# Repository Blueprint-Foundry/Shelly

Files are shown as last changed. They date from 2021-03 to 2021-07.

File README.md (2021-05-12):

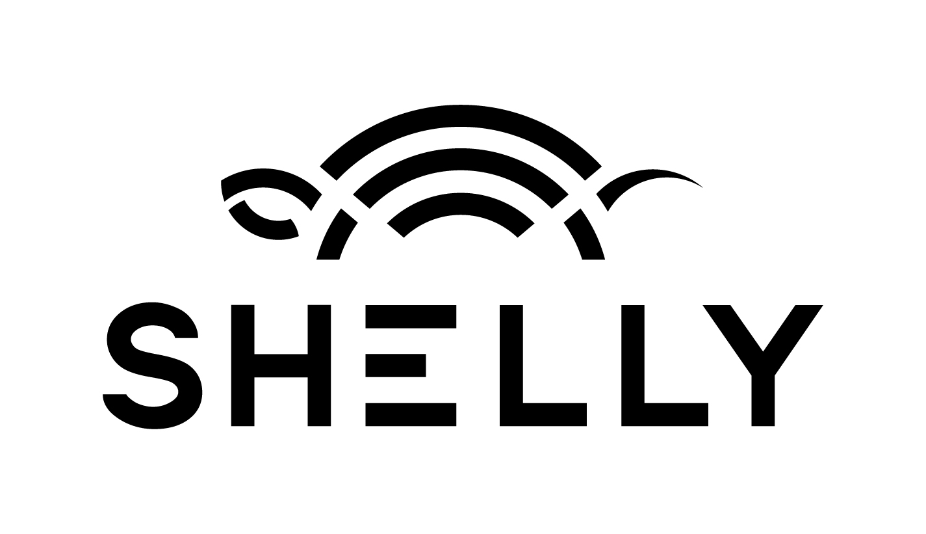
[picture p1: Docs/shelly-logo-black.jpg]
Shelly

Shelly aims to be a low cost ROS robot for teaching and R&amp;D for makers, universities and corporations.



## Links
* Circuitmaker page for the Hardware: https://workspace.circuitmaker.com/Projects/Details/Ilia-Baranov/Shelly

## Dependencies
These must be installed to your environment
* ESP32 Arduino Board Manager https://github.com/espressif/arduino-esp32/blob/master/docs/arduino-ide/boards_manager.md
* Arduino Library https://github.com/bblanchon/ArduinoJson
* Arduino Library https://github.com/Links2004/arduinoWebSockets
* Arduino Library https://github.com/Blueprint-Foundry/Arduino-MAX17055_Driver
* Arduino Library https://github.com/Blueprint-Foundry/PI4IOE5V96248_Arduino_Library
* Arduino Library https://github.com/Blueprint-Foundry/EAAPMST3923A2_Arduino_Library
* Arduino Library https://github.com/pololu/vl53l1x-arduino.git
* Arduino Library https://github.com/sparkfun/SparkFun_ICM-20948_ArduinoLibrary
(note: ensure to enable DMP functionality. Edit ICM_20948_C.h and uncomment line 29: #define ICM_20948_USE_DMP

## Licenses
* Hardware is licensed under Attribution-NonCommercial 4.0 International (CC BY-NC 4.0): https://creativecommons.org/licenses/by-nc/4.0/
* Software is licensed under BSD 3 Clause: https://opensource.org/licenses/BSD-3-Clause
* Documentation is licensed under Attribution-ShareAlike 2.0 Generic (CC BY-SA 2.0): https://creativecommons.org/licenses/by-sa/2.0/
* This project intends to submit for Open Source Hardware certification once ready, this certification mark will be added once successfully granted. https://certification.oshwa.org/
* All rights reserved by Blueprint Foundry.

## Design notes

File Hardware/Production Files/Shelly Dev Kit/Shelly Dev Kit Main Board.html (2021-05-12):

Altium

# Board Information

Date: | | 5/12/2021
Time: | | 10:19:24 AM
Elapsed Time: | | 00:00:00
Filename: | | Shelly Dev Kit Main Board.CMPcbDoc
Units: | | mmmils

General
Horizontal Dimension, max | 3505mils
Vertical Dimension, max | 2125mils
Total surface area
Copper layer count | 2
Smallest electrical gap/space | -
Smallest track width | 1.969mils
Smallest hole size | 12mils
Biggest hole size | 40mils
Number of plated through holes | 182
Number of plated slots | 4
Number of unplated holes | 0
Number of unplated slots | 0
Number of cutouts | 1

Back to top

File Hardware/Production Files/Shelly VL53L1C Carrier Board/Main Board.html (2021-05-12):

Altium

# Board Information

Date: | | 5/12/2021
Time: | | 10:23:28 AM
Elapsed Time: | | 00:00:00
Filename: | | Main Board.CMPcbDoc
Units: | | mmmils

General
Horizontal Dimension, max | 14.5mm
Vertical Dimension, max | 16.5mm
Total surface area
Copper layer count | 2
Smallest electrical gap/space | -
Smallest track width | 0.05mm
Smallest hole size | 0.3048mm
Biggest hole size | 1.016mm
Number of plated through holes | 20
Number of plated slots | 0
Number of unplated holes | 0
Number of unplated slots | 0
Number of cutouts | 1

Back to top

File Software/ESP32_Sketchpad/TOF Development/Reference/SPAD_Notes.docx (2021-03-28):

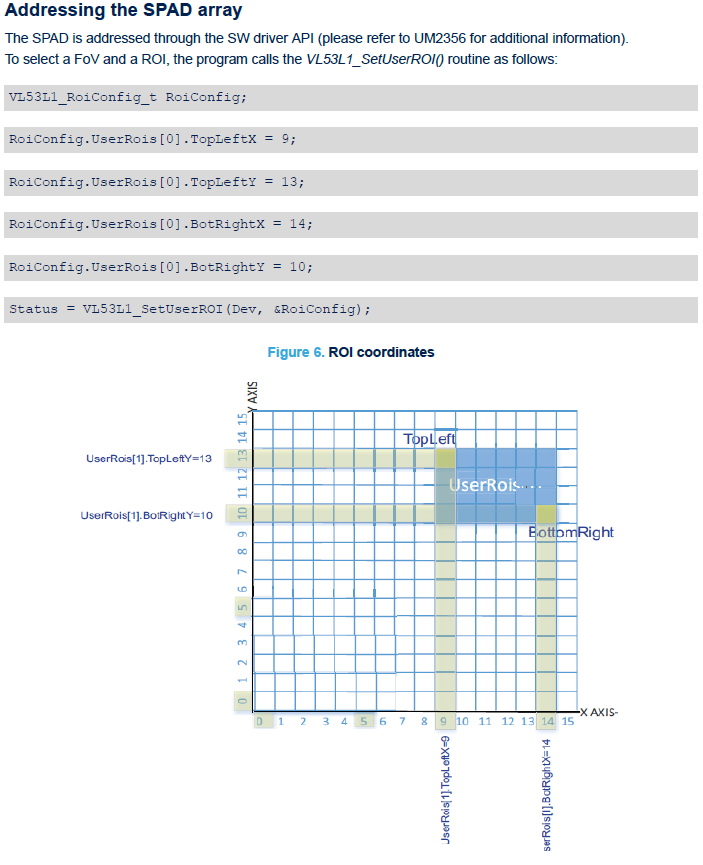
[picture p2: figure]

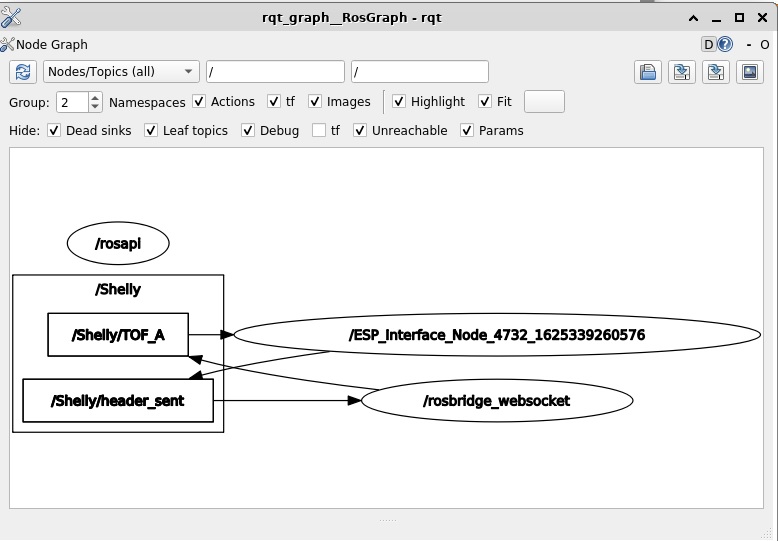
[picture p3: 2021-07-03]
Software/ESP32 Sketchpad/TOF Development/rqt_graph_ESP_interface_node.jpg

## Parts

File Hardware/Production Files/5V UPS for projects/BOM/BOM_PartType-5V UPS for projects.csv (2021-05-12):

Comment | Description | Designator | Quantity | DNP | Octopart URL
Battery | Battery Lithium 3.7V 2.6AH | BT1 | 1 | DNP
Samsung CL10A475MQ8NNNC | CL10 Series 4.7 uF 6.3 V ±20 % Tolerance X5R SMT Multilayer Ceramic Capacitor | C1, C2, C3, C4, C5, C10 | 6 |  | https://octopart.com/cl10a475mq8nnnc-samsung-19831531
Samsung CL05A104KA5NNNC | Ceramic capacitor SMD-0402 100nF /25V X5R# K +-10%, Samsung, RoHS | C6, C11 | 2 |  | https://octopart.com/cl05a104ka5nnnc-samsung-19018960
Samsung Electro-Mechanics CL21A226MOCLRNC | Cap Ceramic 22uF 16V X5R 20% SMD 0805 85°C Cardboard T/R | C7, C8, C9 | 3
Samsung CL05Y474KP5VPNC | Capacitor Ceramic 0.47uF 10% 10V 2-Pin Surface Mount T/R | C12, C13 | 2 |  | https://octopart.com/cl05y474kp5vpnc-samsung-106864824
LTST-C190TBKT | Standard LEDs - SMD WL-SMCD SMD Mono SMD 0603 Blue 465nm | D1 | 1
Lite-On LTST-C190EKT | LED; SMD; 0603; red; 1.12-3mcd; 1.6x0.8x0.8mm; 130°; 2÷2.6V; 10mA | D2 | 1
Lite-On LTST-C190GKT | Green 1.6 x 0.8 x 0.8 mm 130° Water Clear 6 mcd 2.1 V Surface Mount LED | D3 | 1
CUI TB003-500-P02BE | Terminal Block, Screw Type, 5.00 | J1, J2, J5 | 3 |  | https://octopart.com/tb003-500-p02be-cui-100131675
Keystone 54 | Cylindrical Battery Contacts, Clips, Holders & Springs 16-19mm PC BATTERY CLIP | J3, J6 | 2
Adam Tech PH1-05-UA | Conn Unshrouded Header HDR 5 POS 2.54mm Solder ST Thru-Hole | J4 | 1 | DNP | https://octopart.com/ph1-05-ua-adam+tech-7873130
10118194-0001LF | Single Port 5 Contact Horizontal Right Angle Micro B USB 2.0 Receptacle | K1 | 1
Bourns SRN5040TA-1R5M | Ind Power Wirewound 1.5uH 20% Ferrite Core T/R | L1 | 1 |  | https://octopart.com/srn5040ta-1r5m-bourns-95745279
MMBT3906-7-F | MMBT3906 Series PNP 40 V 300 mW Small Signal Transistor Surface Mount- SOT-23-3 | Q1 | 1 |  | https://octopart.com/mmbt3906-7-f-diodes+inc.-39667659
MCU80N03A-TP | N-channel Mosfet, Dpak Package | Q2 | 1 |  | https://octopart.com/mcu80n03a-tp-mcc-110117594
Stackpole Electronics RMCF0603ZT0R00 | RMCF Series 0603 0.1 W 0 Ohm Jumper Surface Mount Thick Film Chip Resistor | R1, R7 | 2 |  | http://octopart.com/rmcf0603zt0r00-stackpole+electronics-19213618
Stackpole Electronics RMCF0402FT3K90 | Res Thick Film 0402 3.9K Ohm 1% 1/16W ±100ppm/°C Molded SMD SMD Paper T/R | R2 | 1 |  | https://octopart.com/rmcf0402ft3k90-stackpole+electronics-21527179
Stackpole Electronics RMCF0603JT680R | Res Thick Film 0603 680 Ohm 5% 0.1W(1/10W) ±200ppm/C Pad SMD Automotive T/R | R3, R6, R8 | 3 |  | https://octopart.com/rmcf0603jt680r-stackpole+electronics-19213592
Stackpole Electronics RMCF0402FT22K1 | Res Thick Film 0402 22.1K Ohm 1% 0.063W ±100ppm/°C Molded SMD Paper T/R | R4, R12 | 2 |  | https://octopart.com/rmcf0402ft22k1-stackpole+electronics-19211363
Stackpole Electronics RMCF0402FT511R | Res Thick Film 0402 511 Ohm 1% 0.063W(1/16W) ±100ppm/C Pad SMD Automotive T/R | R5, R11 | 2 |  | https://octopart.com/rmcf0402ft511r-stackpole+electronics-19212568
Stackpole Electronics RMCF0603FT2K00 | Res Thick Film 0603 2K Ohm 1% 0.1W(1/10W) ±100ppm/C Pad SMD Automotive T/R | R9 | 1 |  | https://octopart.com/rmcf0603ft2k00-stackpole+electronics-19213115
Stackpole Electronics RMCF0402FT2K55 | Res Thick Film 0402 2.55K Ohm 1% 0.063W ±100ppm/°C Molded SMD Paper T/R | R10 | 1 |  | https://octopart.com/rmcf0402ft2k55-stackpole+electronics-19211346
Stackpole Electronics RMCF0402FT33K0 | Res Thick Film 0402 33K Ohm 1% 0.063W(1/16W) ±100ppm/C Pad SMD Automotive T/R | R13 | 1 |  | https://octopart.com/rmcf0402ft33k0-stackpole+electronics-19212474
Stackpole Electronics RMCF0402FT2K00 | Res Thick Film 0402 2K Ohm 1% 0.063W(1/16W) ±100ppm/C Pad SMD Automotive T/R | R14 | 1 |  | https://octopart.com/rmcf0402ft2k00-stackpole+electronics-19212433
Stackpole Electronics RMCF0603FT215R | Res Thick Film 0603 215 Ohm 1% 0.1W(1/10W) ±100ppm/C Pad SMD Automotive T/R | R15 | 1 |  | https://octopart.com/rmcf0603ft215r-stackpole+electronics-19211080
Stackpole Electronics RMCF0402JT10K0 | Res Thick Film 0402 10K Ohm 5% 0.063W(1/16W) ±100ppm/C Pad SMD Automotive T/R | R16, R17 | 2 |  | https://octopart.com/rmcf0402jt10k0-stackpole+electronics-19212679
Cyntec RL1632T4F-R010-FNH | Res 0.01 Ohm 1% 1W 1206 | R18 | 1 |  | https://octopart.com/rl1632t4f-r010-fnh-cyntec-86610802
C&K Components OS102011MS2QN1 | Switch; Slide; Mini; SPDT; ON-ON; Non-Shorting(BBM); 100mA; 12VDC; ThruHole; PC Pin | SW1, SW2 | 2 |  | https://octopart.com/os102011ms2qn1-c%26k+components-2486956
TPS2121RUXR | 2.7-22V, 56m?, 4.5A, Priority Power MUX with Seamless Switchover 12-VQFN-HR -40 to 125 | U1 | 1 |  | https://octopart.com/tps2121ruxr-texas+instruments-95511053
Texas Instruments TPS259571DSGR | TPS259571 12V eFuse with Fast Overvoltage Protection 2.7V to 18V 4A 34m Ohm 8-Pin WSON T/R | U2 | 1 |  | https://octopart.com/tps259571dsgr-texas+instruments-88135752
MCP73831T-2DCI/OT | Microchip MCP73831T-2DCI/OT; Battery Charge Controller; 500mA; 5-Pin SOT-23 | U3 | 1 |  | https://octopart.com/mcp73831t-2dci%2Fot-microchip-422782
MAX17055ETB+T | MAX17055 Series 4.9 V 18 uA Stand-Alone ModelGauge m5 Fuel Gauge - TDFN-10 | U4 | 1 |  | https://octopart.com/max17055etb%2Bt-maxim+integrated-76519097
RT4812GJ8F | Boost Switching Regulator IC Positive Adjustable 1.8V 1 Output 2A SOT-23-8 Thin, TSOT-23-8 | U5 | 1

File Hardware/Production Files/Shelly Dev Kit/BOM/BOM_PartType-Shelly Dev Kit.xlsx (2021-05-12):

Comment | Description | Manufacturer Part Number | Octopart URL | Designator | Quantity | DNP
ESP32-WROVER-E (8MB) | Rx Txrx Mod Wifi Pcb Trace SMD | ESP32-WROVER-E (8MB) | https://octopart.com/esp32-wrover-e+%288mb%29-espressif+systems-108216292 | A1 | 1
Everlight EAAPMST3923A2 | Ambient Light Sensor | EAAPMST3923A2 |  | A2 | 1
1uF | CAP CER 1UF 16V 10% X5R 0603 |  | https://octopart.com/0603yd105kat2a-avx+interconnect+%2F+elco-46506197 | C1, C2, C3, C4, C5, C10, C13 | 7
Samsung Electro-Mechanics CL21A226MOCLRNC | Cap Ceramic 22uF 16V X5R 20% SMD 0805 85°C Cardboard T/R | CL21A226MOCLRNC |  | C6, C8, C12, C14 | 4
Taiyo Yuden TMK105BJ223KV-F | Multilayer Ceramic Capacitors (High dielectric type), 25V, 0.022 uF, ± 10 %, 0402, X5R/B, RoHS | TMK105BJ223KV-F | https://octopart.com/tmk105bj223kv-f-taiyo+yuden-23272753 | C7 | 1
Samsung CL05A104KA5NNNC | Ceramic capacitor SMD-0402 100nF /25V X5R# K +-10%, Samsung, RoHS | CL05A104KA5NNNC | https://octopart.com/cl05a104ka5nnnc-samsung-19018960 | C9, C11 | 2
Seeed Studio 601000200 | Address Led Discret Serial R/g/b | 601000200 | https://octopart.com/601000200-seeed+studio-88826571 | D1, D2 | 2
JST (JAPAN SOLDERLESS TERMINALS) B5B-XH-A(LF)(SN) | CONN HEADER XH TOP 5POS 2.5MM | B5B-XH-A(LF)(SN) | https://octopart.com/b5b-xh-a%28lf%29%28sn%29-jst-3990208 | J1 | 1
Global Connector Technology BG302-05-A-L-G | Board to Board, Receptacle, 5 Position, 1ROW | BG302-05-A-L-G | https://octopart.com/bg302-05-a-l-g-global+connector+technology-22009391 | J2 | 1
Amphenol ICC / FCI SFV24R-3STE1HLF | SFV24R-3STE1HLF-FFC/FPC Conn Rohs Compliant: Yes | SFV24R-3STE1HLF | https://octopart.com/sfv24r-3ste1hlf-amphenol+icc+%2F+fci-22289564 | J3 | 1
Adam Tech PH1-05-UA | Conn Unshrouded Header HDR 5 POS 2.54mm Solder ST Thru-Hole | PH1-05-UA | https://octopart.com/ph1-05-ua-adam+tech-7873130 | J4, J5 | 2 | DNP
10118194-0001LF | Single Port 5 Contact Horizontal Right Angle Micro B USB 2.0 Receptacle |  |  | K1 | 1
MMBT3904 | TRANS NPN 40V 0.2A SOT23 |  | https://octopart.com/mmbt3904%2C215-nxp+semiconductors-10477684 | Q1, Q2 | 2
Nexperia 2N7002NXAKR | 2N7002NXAK - 60 V, single N-channel Trench MOSFET | 2N7002NXAKR | https://octopart.com/2n7002nxakr-nexperia-103147780 | Q3, Q4 | 2
10k | RES SMD 10K OHM 5% 1/10W 0603 | RC1608J103CS | http://octopart.com/rc1608j103cs-samsung-2405586 | R1, R2, R5, R6, R7, R8, R9, R14, R15, R16, R17, R18, R19 | 13
27R | YAGEO (PHYCOMP) RC0603JR-0727RL RESISTOR, RC21 0603 27R |  | http://octopart.com/rc0603jr-0727rl-yageo-40953074 | R3, R4 | 2
Stackpole Electronics RMCF0402JT1K00 | Res Thick Film 0402 1K Ohm 5% 0.063W(1/16W) ±100ppm/C Pad SMD Automotive T/R | RMCF0402JT1K00 | https://octopart.com/rmcf0402jt1k00-stackpole+electronics-19212695 | R10, R13, R20 | 3
Ohmite KDV12DR200ET | 0.2 Ohm 1206 0.5% 0.5W Rohs Compliant: Yes | KDV12DR200ET | https://octopart.com/kdv12dr200et-ohmite-103743653 | R11, R12 | 2
C&K Components PTS636 SL50 SMTR LFS | Switch Tactile N.O. SPST Rectangular Button Gull Wing 0.05A 12VDC 1.27N SMD T/R | PTS636 SL50 SMTR LFS | https://octopart.com/pts636+sl50+smtr+lfs-c%26k+components-100131649 | SW1 | 1
Diodes AP2112K-3.3TRG1 | AP2112 Series 0.6 A 3.3 V Fixed Output SMT LDO Linear Regulator - SOT23-5 | AP2112K-3.3TRG1 | http://octopart.com/ap2112k-3.3trg1-diodes+inc.-30954557 | U1 | 1
MIC5392 | MIC5392 Series 2.8 / 1.8 V 150 mA Surface Mount Dual LDO Regulator - TDFN-6 | MIC5392-MGYMT-TR |  | U2 | 1
Future Technology Devices International (FTDI) FT231XS-R | USB Full Speed to Full Handshake UART with USB Charger Detection | FT231XS-R | http://octopart.com/ft231xs-r-ftdi-22061507 | U3 | 1
STMicroelectronics STSPIN220 | STSPIN220 Series 10 V Quad Surface Mount Stepper Motor Driver - VFQFPN-16 | STSPIN220 | https://octopart.com/stspin220-stmicroelectronics-74146215 | U4 | 1
ICM-20948 | ICM-20948 - World's Lowest Power 9-Axis MEMS MotionTracking Device | ICM-20948 | https://octopart.com/icm-20948-invensense-73011870 | U5 | 1
Analog Devices LTC4311CSC6#TRPBF | I2C Logic Buffer 1.8V/2.5V/3.3V/5V Automotive 6-Pin SC-70 T/R |  |  | U6 | 1
Diodes Inc. PI4IOE5V96248ZLEX | Interface IO Expander TQFN7070-56 T&R 3K | PI4IOE5V96248ZLEX | https://octopart.com/pi4ioe5v96248zlex-diodes+inc.-87342265 | U7 | 1

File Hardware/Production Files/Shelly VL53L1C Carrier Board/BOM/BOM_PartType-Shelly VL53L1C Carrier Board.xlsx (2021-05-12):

Comment | Description | Designator | DNP | Quantity
STMicroelectronics VL53L1CXV0FY/1 | Proximity Sensor Environmental 4mm 2.6V to 3.5VDC 12-Pin LGA T/R | A1 |  | 1
Samsung CL10A475MQ8NNNC | CL10 Series 4.7 uF 6.3 V ±20 % Tolerance X5R SMT Multilayer Ceramic Capacitor | C1, C3, C4 |  | 3
Samsung CL05A104KA5NNNC | Ceramic capacitor SMD-0402 100nF /25V X5R# K +-10%, Samsung, RoHS | C2 |  | 1
Adam Tech PH1-05-UA | Conn Unshrouded Header HDR 5 POS 2.54mm Solder ST Thru-Hole | J1 | DNP | 1
Nexperia 2N7002NXAKR | 2N7002NXAK - 60 V, single N-channel Trench MOSFET | Q1, Q2 |  | 2
Stackpole Electronics RMCF0402JT10K0 | Res Thick Film 0402 10K Ohm 5% 0.063W(1/16W) ±100ppm/C Pad SMD Automotive T/R | R1, R4, R6 |  | 3
Stackpole Electronics RMCF0402JT1K00 | Res Thick Film 0402 1K Ohm 5% 0.063W(1/16W) ±100ppm/C Pad SMD Automotive T/R | R2 |  | 1
Stackpole Electronics RMCF0402JT10K0 | Res Thick Film 0402 10K Ohm 5% 0.063W(1/16W) ±100ppm/C Pad SMD Automotive T/R | R3, R5 | DNP | 2
Microchip MIC5504-2.8YM5-TR | Single 300mA LDO with Enable Pull-Down & Auto Discharge 5 SOT-23 T/R RoHS Compliant: Yes | U1 |  | 1

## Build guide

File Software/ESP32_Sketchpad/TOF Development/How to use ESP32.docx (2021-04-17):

https://github.com/espressif/arduino-esp32

install json using Arduino IDE Boards Manager

https://github.com/espressif/arduino-esp32/blob/master/docs/arduino-ide/boards_manager.md

open Arduino IDE

Go to File → Preferences

Add https://raw.githubusercontent.com/espressif/arduino-esp32/gh-pages/package_esp32_index.json to additional board manager URLS

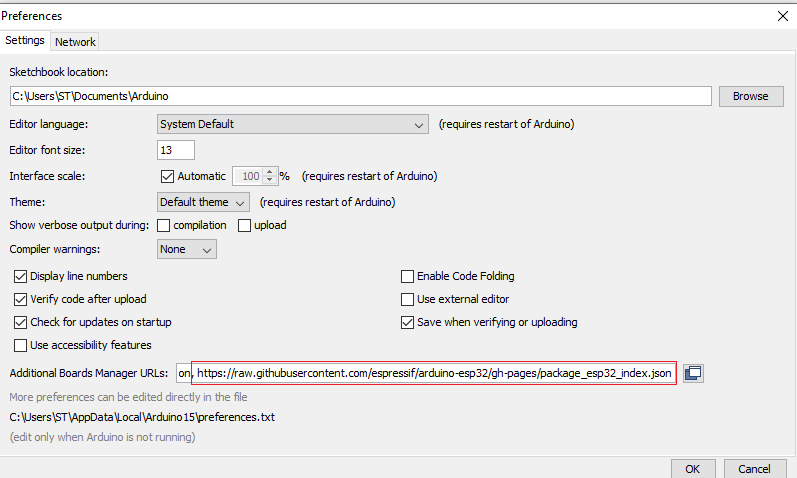
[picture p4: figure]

Tools → Board Manager

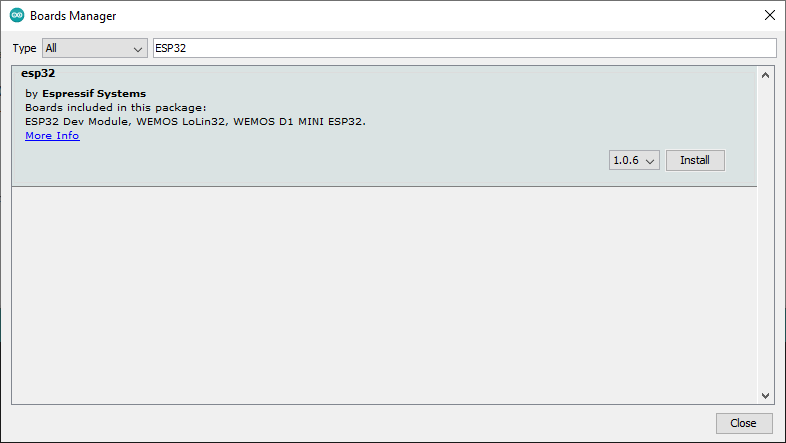
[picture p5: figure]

Press install

Select the board

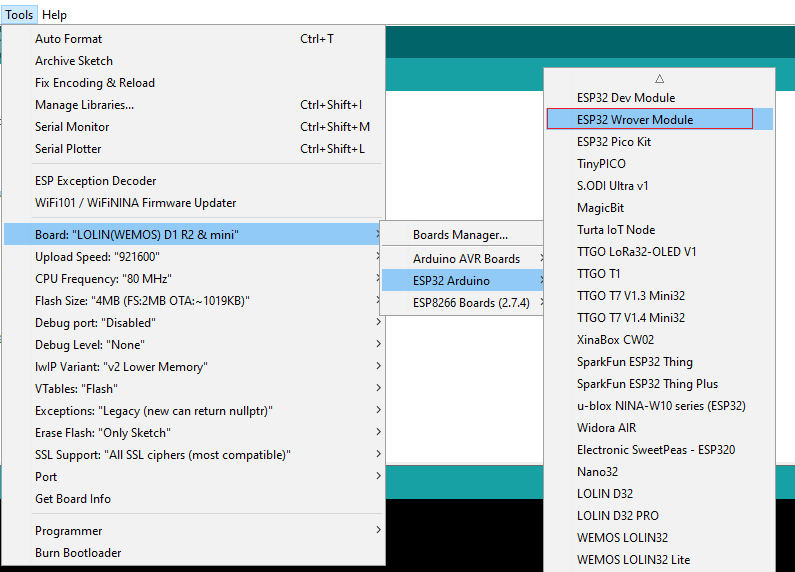
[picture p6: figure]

Install “cp2104 usb to uart bridge controller” driver

https://www.silabs.com/developers/usb-to-uart-bridge-vcp-drivers

Device manager, find new com port, in Arduino IDE go to Tools → port

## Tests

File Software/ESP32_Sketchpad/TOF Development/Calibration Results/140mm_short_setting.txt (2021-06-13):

VL53L1X is initialized
original width: 16, original height: 16 
original center: 199 
new width: 16, new height: 16 
new center: 199 
Calculating true distances given 140.000000 mm away flat surface 
t:-3, p: -3, L2R_T2B_distances[0] = 144.464569 
t:-3, p: -1, L2R_T2B_distances[1] = 142.461853 
t:-3, p: 1, L2R_T2B_distances[2] = 142.461853 
t:-3, p: 3, L2R_T2B_distances[3] = 144.464569 
t:-1, p: -3, L2R_T2B_distances[4] = 142.461853 
t:-1, p: -1, L2R_T2B_distances[5] = 140.486893 
t:-1, p: 1, L2R_T2B_distances[6] = 140.486893 
t:-1, p: 3, L2R_T2B_distances[7] = 142.461853 
t:1, p: -3, L2R_T2B_distances[8] = 142.461853 
t:1, p: -1, L2R_T2B_distances[9] = 140.486893 
t:1, p: 1, L2R_T2B_distances[10] = 140.486893 
t:1, p: 3, L2R_T2B_distances[11] = 142.461853 
t:3, p: -3, L2R_T2B_distances[12] = 144.464569 
t:3, p: -1, L2R_T2B_distances[13] = 142.461853 
t:3, p: 1, L2R_T2B_distances[14] = 142.461853 
t:3, p: 3, L2R_T2B_distances[15] = 144.464569 
Taking 50 samples of each 16 ROIs to find average reported distance... 
sample: 0 
sample: 1 
sample: 2 
sample: 3 
sample: 4 
sample: 5 
sample: 6 
sample: 7 
sample: 8 
sample: 9 
sample: 10 
sample: 11 
sample: 12 
sample: 13 
sample: 14 
sample: 15 
sample: 16 
sample: 17 
sample: 18 
sample: 19 
sample: 20 
sample: 21 
sample: 22 
sample: 23 
sample: 24 
sample: 25 
sample: 26 
sample: 27 
sample: 28 
sample: 29 
sample: 30 
sample: 31 
sample: 32 
sample: 33 
sample: 34 
sample: 35 
sample: 36 
sample: 37 
sample: 38 
sample: 39 
sample: 40 
sample: 41 
sample: 42 
sample: 43 
sample: 44 
sample: 45 
sample: 46 
sample: 47 
sample: 48 
sample: 49 
find offsets between average and true distances and save in EEPROM... 
spad_avg: 165.520020, real: 144.464569, calibrated_differences[0]: -21.000000 
spad_avg: 144.220047, real: 142.461853, calibrated_differences[1]: -1.000000 
spad_avg: 151.620010, real: 142.461853, calibrated_differences[2]: -9.000000 
spad_avg: 170.780060, real: 144.464569, calibrated_differences[3]: -26.000000 
spad_avg: 140.999985, real: 142.461853, calibrated_differences[4]: 1.000000 
spad_avg: 115.979996, real: 140.486893, calibrated_differences[5]: 24.000000 
spad_avg: 123.479988, real: 140.486893, calibrated_differences[6]: 17.000000 
spad_avg: 158.019989, real: 142.461853, calibrated_differences[7]: -15.000000 
spad_avg: 140.460007, real: 142.461853, calibrated_differences[8]: 2.000000 
spad_avg: 117.059998, real: 140.486893, calibrated_differences[9]: 23.000000 
spad_avg: 120.180016, real: 140.486893, calibrated_differences[10]: 20.000000 
spad_avg: 149.739990, real: 142.461853, calibrated_differences[11]: -7.000000 
spad_avg: 165.319977, real: 144.464569, calibrated_differences[12]: -20.000000 
spad_avg: 137.220001, real: 142.461853, calibrated_differences[13]: 5.000000 
spad_avg: 140.059998, real: 142.461853, calibrated_differences[14]: 2.000000 
spad_avg: 165.259995, real: 144.464569, calibrated_differences[15]: -20.000000 
EEPROM readback data[0]: -21 
EEPROM readback data[1]: -1 
EEPROM readback data[2]: -9 
EEPROM readback data[3]: -26 
EEPROM readback data[4]: 1 
EEPROM readback data[5]: 24 
EEPROM readback data[6]: 17 
EEPROM readback data[7]: -15 
EEPROM readback data[8]: 2 
EEPROM readback data[9]: 23 
EEPROM readback data[10]: 20 
EEPROM readback data[11]: -7 
EEPROM readback data[12]: -20 
EEPROM readback data[13]: 5 
EEPROM readback data[14]: 2 
EEPROM readback data[15]: -20 
left2right_top2down_spad_centers[0] = 145, uncalibrated distance is: 164 
calibrated_offsets[0] = -21,                 calibrated distance is: 143 
left2right_top2down_spad_centers[1] = 177, uncalibrated distance is: 145 
calibrated_offsets[1] = -1,                 calibrated distance is: 144 
left2right_top2down_spad_centers[2] = 209, uncalibrated distance is: 154 
calibrated_offsets[2] = -9,                 calibrated distance is: 145 
left2right_top2down_spad_centers[3] = 241, uncalibrated distance is: 176 
calibrated_offsets[3] = -26,                 calibrated distance is: 150 
left2right_top2down_spad_centers[4] = 149, uncalibrated distance is: 139 
calibrated_offsets[4] = 1,                 calibrated distance is: 140 
left2right_top2down_spad_centers[5] = 181, uncalibrated distance is: 117 
calibrated_offsets[5] = 24,                 calibrated distance is: 141 
left2right_top2down_spad_centers[6] = 213, uncalibrated distance is: 122 
calibrated_offsets[6] = 17,                 calibrated distance is: 139 
left2right_top2down_spad_centers[7] = 245, uncalibrated distance is: 159 
calibrated_offsets[7] = -15,                 calibrated distance is: 144 
left2right_top2down_spad_centers[8] = 110, uncalibrated distance is: 142 
calibrated_offsets[8] = 2,                 calibrated distance is: 144 
left2right_top2down_spad_centers[9] = 78, uncalibrated distance is: 118 
calibrated_offsets[9] = 23,                 calibrated distance is: 141 
left2right_top2down_spad_centers[10] = 46, uncalibrated distance is: 120 
calibrated_offsets[10] = 20,                 calibrated distance is: 140 
left2right_top2down_spad_centers[11] = 14, uncalibrated distance is: 152 
calibrated_offsets[11] = -7,                 calibrated distance is: 145 
left2right_top2down_spad_centers[12] = 106, uncalibrated distance is: 160 
calibrated_offsets[12] = -20,                 calibrated distance is: 140 
left2right_top2down_spad_centers[13] = 74, uncalibrated distance is: 138 
calibrated_offsets[13] = 5,                 calibrated distance is: 143 
left2right_top2down_spad_centers[14] = 42, uncalibrated distance is: 137 
calibrated_offsets[14] = 2,                 calibrated distance is: 139 
left2right_top2down_spad_centers[15] = 10, uncalibrated distance is: 163 
calibrated_offsets[15] = -20,                 calibrated distance is: 143

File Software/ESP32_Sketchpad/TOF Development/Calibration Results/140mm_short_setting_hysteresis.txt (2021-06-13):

EEPROM readback data[0]: -22 
EEPROM readback data[1]: -2 
EEPROM readback data[2]: -8 
EEPROM readback data[3]: -25 
EEPROM readback data[4]: 2 
EEPROM readback data[5]: 24 
EEPROM readback data[6]: 16 
EEPROM readback data[7]: -14 
EEPROM readback data[8]: 1 
EEPROM readback data[9]: 23 
EEPROM readback data[10]: 19 
EEPROM readback data[11]: -8 
EEPROM readback data[12]: -20 
EEPROM readback data[13]: 5 
EEPROM readback data[14]: 2 
EEPROM readback data[15]: -20 

---

EEPROM readback data[0]: -21 
EEPROM readback data[1]: -2 
EEPROM readback data[2]: -9 
EEPROM readback data[3]: -26 
EEPROM readback data[4]: 2 
EEPROM readback data[5]: 24 
EEPROM readback data[6]: 16 
EEPROM readback data[7]: -15 
EEPROM readback data[8]: 2 
EEPROM readback data[9]: 22 
EEPROM readback data[10]: 20 
EEPROM readback data[11]: -7 
EEPROM readback data[12]: -20 
EEPROM readback data[13]: 5 
EEPROM readback data[14]: 2 
EEPROM readback data[15]: -21

VL53L1X is initialized
original width: 16, original height: 16 
original center: 199 
new width: 16, new height: 16 
new center: 199 
Calculating true distances given 140.000000 mm away flat surface 
t:-3, p: -3, L2R_T2B_distances[0] = 144.464569 
t:-3, p: -1, L2R_T2B_distances[1] = 142.461853 
t:-3, p: 1, L2R_T2B_distances[2] = 142.461853 
t:-3, p: 3, L2R_T2B_distances[3] = 144.464569 
t:-1, p: -3, L2R_T2B_distances[4] = 142.461853 
t:-1, p: -1, L2R_T2B_distances[5] = 140.486893 
t:-1, p: 1, L2R_T2B_distances[6] = 140.486893 
t:-1, p: 3, L2R_T2B_distances[7] = 142.461853 
t:1, p: -3, L2R_T2B_distances[8] = 142.461853 
t:1, p: -1, L2R_T2B_distances[9] = 140.486893 
t:1, p: 1, L2R_T2B_distances[10] = 140.486893 
t:1, p: 3, L2R_T2B_distances[11] = 142.461853 
t:3, p: -3, L2R_T2B_distances[12] = 144.464569 
t:3, p: -1, L2R_T2B_distances[13] = 142.461853 
t:3, p: 1, L2R_T2B_distances[14] = 142.461853 
t:3, p: 3, L2R_T2B_distances[15] = 144.464569 
Taking 50 samples of each 16 ROIs to find average reported distance... 
sample: 0 
sample: 1 
sample: 2 
sample: 3 
sample: 4 
sample: 5 
sample: 6 
sample: 7 
sample: 8 
sample: 9 
sample: 10 
sample: 11 
sample: 12 
sample: 13 
sample: 14 
sample: 15 
sample: 16 
sample: 17 
sample: 18 
sample: 19 
sample: 20 
sample: 21 
sample: 22 
sample: 23 
sample: 24 
sample: 25 
sample: 26 
sample: 27 
sample: 28 
sample: 29 
sample: 30 
sample: 31 
sample: 32 
sample: 33 
sample: 34 
sample: 35 
sample: 36 
sample: 37 
sample: 38 
sample: 39 
sample: 40 
sample: 41 
sample: 42 
sample: 43 
sample: 44 
sample: 45 
sample: 46 
sample: 47 
sample: 48 
sample: 49 
find offsets between average and true distances and save in EEPROM... 
spad_avg: 166.360016, real: 144.464569, calibrated_differences[0]: -21.000000 
spad_avg: 144.900009, real: 142.461853, calibrated_differences[1]: -2.000000 
spad_avg: 151.840027, real: 142.461853, calibrated_differences[2]: -9.000000 
spad_avg: 170.900024, real: 144.464569, calibrated_differences[3]: -26.000000 
spad_avg: 140.240021, real: 142.461853, calibrated_differences[4]: 2.000000 
spad_avg: 116.419998, real: 140.486893, calibrated_differences[5]: 24.000000 
spad_avg: 123.719986, real: 140.486893, calibrated_differences[6]: 16.000000 
spad_avg: 157.800003, real: 142.461853, calibrated_differences[7]: -15.000000 
spad_avg: 139.560043, real: 142.461853, calibrated_differences[8]: 2.000000 
spad_avg: 118.220001, real: 140.486893, calibrated_differences[9]: 22.000000 
spad_avg: 120.060005, real: 140.486893, calibrated_differences[10]: 20.000000 
spad_avg: 149.760025, real: 142.461853, calibrated_differences[11]: -7.000000 
spad_avg: 164.979950, real: 144.464569, calibrated_differences[12]: -20.000000 
spad_avg: 137.020004, real: 142.461853, calibrated_differences[13]: 5.000000 
spad_avg: 139.739960, real: 142.461853, calibrated_differences[14]: 2.000000 
spad_avg: 165.839966, real: 144.464569, calibrated_differences[15]: -21.000000 
EEPROM readback data[0]: -21 
EEPROM readback data[1]: -2 
EEPROM readback data[2]: -9 
EEPROM readback data[3]: -26 
EEPROM readback data[4]: 2 
EEPROM readback data[5]: 24 
EEPROM readback data[6]: 16 
EEPROM readback data[7]: -15 
EEPROM readback data[8]: 2 
EEPROM readback data[9]: 22 
EEPROM readback data[10]: 20 
EEPROM readback data[11]: -7 
EEPROM readback data[12]: -20 
EEPROM readback data[13]: 5 
EEPROM readback data[14]: 2 
EEPROM readback data[15]: -21 
left2right_top2down_spad_centers[0] = 145, uncalibrated distance is: 166 
calibrated_offsets[0] = -21,                 calibrated distance is: 145 
left2right_top2down_spad_centers[1] = 177, uncalibrated distance is: 143 
calibrated_offsets[1] = -2,                 calibrated distance is: 141 
left2right_top2down_spad_centers[2] = 209, uncalibrated distance is: 150 
calibrated_offsets[2] = -9,                 calibrated distance is: 141 
left2right_top2down_spad_centers[3] = 241, uncalibrated distance is: 172 
calibrated_offsets[3] = -26,                 calibrated distance is: 146 
left2right_top2down_spad_centers[4] = 149, uncalibrated distance is: 138 
calibrated_offsets[4] = 2,                 calibrated distance is: 140 
left2right_top2down_spad_centers[5] = 181, uncalibrated distance is: 117 
calibrated_offsets[5] = 24,                 calibrated distance is: 141 
left2right_top2down_spad_centers[6] = 213, uncalibrated distance is: 123 
calibrated_offsets[6] = 16,                 calibrated distance is: 139 
left2right_top2down_spad_centers[7] = 245, uncalibrated distance is: 160 
calibrated_offsets[7] = -15,                 calibrated distance is: 145 
left2right_top2down_spad_centers[8] = 110, uncalibrated distance is: 140 
calibrated_offsets[8] = 2,                 calibrated distance is: 142 
left2right_top2down_spad_centers[9] = 78, uncalibrated distance is: 119 
calibrated_offsets[9] = 22,                 calibrated distance is: 141 
left2right_top2down_spad_centers[10] = 46, uncalibrated distance is: 121 
calibrated_offsets[10] = 20,                 calibrated distance is: 141 
left2right_top2down_spad_centers[11] = 14, uncalibrated distance is: 148 
calibrated_offsets[11] = -7,                 calibrated distance is: 141 
left2right_top2down_spad_centers[12] = 106, uncalibrated distance is: 161 
calibrated_offsets[12] = -20,                 calibrated distance is: 141 
left2right_top2down_spad_centers[13] = 74, uncalibrated distance is: 138 
calibrated_offsets[13] = 5,                 calibrated distance is: 143 
left2right_top2down_spad_centers[14] = 42, uncalibrated distance is: 141 
calibrated_offsets[14] = 2,                 calibrated distance is: 143 
left2right_top2down_spad_centers[15] = 10, uncalibrated distance is: 163 
calibrated_offsets[15] = -21,                 calibrated distance is: 142

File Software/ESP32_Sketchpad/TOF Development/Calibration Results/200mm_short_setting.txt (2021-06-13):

with lights on:

EEPROM readback data[0]: -23 
EEPROM readback data[1]: -6 
EEPROM readback data[2]: -6 
EEPROM readback data[3]: -24 
EEPROM readback data[4]: -1 
EEPROM readback data[5]: 23 
EEPROM readback data[6]: 22 
EEPROM readback data[7]: -7 
EEPROM readback data[8]: 0 
EEPROM readback data[9]: 25 
EEPROM readback data[10]: 24 
EEPROM readback data[11]: -6 
EEPROM readback data[12]: -16 
EEPROM readback data[13]: 1 
EEPROM readback data[14]: 3 
EEPROM readback data[15]: -18 

with lights off:

EEPROM readback data[0]: -23 
EEPROM readback data[1]: -6 
EEPROM readback data[2]: -6 
EEPROM readback data[3]: -26 
EEPROM readback data[4]: -1 
EEPROM readback data[5]: 24 
EEPROM readback data[6]: 21 
EEPROM readback data[7]: -8 
EEPROM readback data[8]: 0 
EEPROM readback data[9]: 25 
EEPROM readback data[10]: 25 
EEPROM readback data[11]: -5 
EEPROM readback data[12]: -15 
EEPROM readback data[13]: 1 
EEPROM readback data[14]: 3 
EEPROM readback data[15]: -18 

------

VL53L1X is initialized
original width: 16, original height: 16 
original center: 199 
new width: 16, new height: 16 
new center: 199 
Calculating true distances given 200.000000 mm away flat surface 
t:-3, p: -3, L2R_T2B_distances[0] = 206.377975 
t:-3, p: -1, L2R_T2B_distances[1] = 203.516937 
t:-3, p: 1, L2R_T2B_distances[2] = 203.516937 
t:-3, p: 3, L2R_T2B_distances[3] = 206.377975 
t:-1, p: -3, L2R_T2B_distances[4] = 203.516937 
t:-1, p: -1, L2R_T2B_distances[5] = 200.695557 
t:-1, p: 1, L2R_T2B_distances[6] = 200.695557 
t:-1, p: 3, L2R_T2B_distances[7] = 203.516937 
t:1, p: -3, L2R_T2B_distances[8] = 203.516937 
t:1, p: -1, L2R_T2B_distances[9] = 200.695557 
t:1, p: 1, L2R_T2B_distances[10] = 200.695557 
t:1, p: 3, L2R_T2B_distances[11] = 203.516937 
t:3, p: -3, L2R_T2B_distances[12] = 206.377975 
t:3, p: -1, L2R_T2B_distances[13] = 203.516937 
t:3, p: 1, L2R_T2B_distances[14] = 203.516937 
t:3, p: 3, L2R_T2B_distances[15] = 206.377975 
Taking 50 samples of each 16 ROIs to find average reported distance... 
sample: 0 
sample: 1 
sample: 2 
sample: 3 
sample: 4 
sample: 5 
sample: 6 
sample: 7 
sample: 8 
sample: 9 
sample: 10 
sample: 11 
sample: 12 
sample: 13 
sample: 14 
sample: 15 
sample: 16 
sample: 17 
sample: 18 
sample: 19 
sample: 20 
sample: 21 
sample: 22 
sample: 23 
sample: 24 
sample: 25 
sample: 26 
sample: 27 
sample: 28 
sample: 29 
sample: 30 
sample: 31 
sample: 32 
sample: 33 
sample: 34 
sample: 35 
sample: 36 
sample: 37 
sample: 38 
sample: 39 
sample: 40 
sample: 41 
sample: 42 
sample: 43 
sample: 44 
sample: 45 
sample: 46 
sample: 47 
sample: 48 
sample: 49 
find offsets between average and true distances and save in EEPROM... 
spad_avg: 229.540039, real: 206.377975, calibrated_differences[0]: -23.000000 
spad_avg: 210.419998, real: 203.516937, calibrated_differences[1]: -6.000000 
spad_avg: 210.280014, real: 203.516937, calibrated_differences[2]: -6.000000 
spad_avg: 233.320007, real: 206.377975, calibrated_differences[3]: -26.000000 
spad_avg: 205.259964, real: 203.516937, calibrated_differences[4]: -1.000000 
spad_avg: 176.259964, real: 200.695557, calibrated_differences[5]: 24.000000 
spad_avg: 179.580063, real: 200.695557, calibrated_differences[6]: 21.000000 
spad_avg: 211.519989, real: 203.516937, calibrated_differences[7]: -8.000000 
spad_avg: 204.179993, real: 203.516937, calibrated_differences[8]: 0.000000 
spad_avg: 174.940002, real: 200.695557, calibrated_differences[9]: 25.000000 
spad_avg: 175.439957, real: 200.695557, calibrated_differences[10]: 25.000000 
spad_avg: 209.080002, real: 203.516937, calibrated_differences[11]: -5.000000 
spad_avg: 222.339920, real: 206.377975, calibrated_differences[12]: -15.000000 
spad_avg: 202.059982, real: 203.516937, calibrated_differences[13]: 1.000000 
spad_avg: 199.860016, real: 203.516937, calibrated_differences[14]: 3.000000 
spad_avg: 224.539978, real: 206.377975, calibrated_differences[15]: -18.000000 
EEPROM readback data[0]: -23 
EEPROM readback data[1]: -6 
EEPROM readback data[2]: -6 
EEPROM readback data[3]: -26 
EEPROM readback data[4]: -1 
EEPROM readback data[5]: 24 
EEPROM readback data[6]: 21 
EEPROM readback data[7]: -8 
EEPROM readback data[8]: 0 
EEPROM readback data[9]: 25 
EEPROM readback data[10]: 25 
EEPROM readback data[11]: -5 
EEPROM readback data[12]: -15 
EEPROM readback data[13]: 1 
EEPROM readback data[14]: 3 
EEPROM readback data[15]: -18 
left2right_top2down_spad_centers[0] = 145, uncalibrated distance is: 232 
calibrated_offsets[0] = -23,                 calibrated distance is: 209 
left2right_top2down_spad_centers[1] = 177, uncalibrated distance is: 211 
calibrated_offsets[1] = -6,                 calibrated distance is: 205 
left2right_top2down_spad_centers[2] = 209, uncalibrated distance is: 209 
calibrated_offsets[2] = -6,                 calibrated distance is: 203 
left2right_top2down_spad_centers[3] = 241, uncalibrated distance is: 233 
calibrated_offsets[3] = -26,                 calibrated distance is: 207 
left2right_top2down_spad_centers[4] = 149, uncalibrated distance is: 204 
calibrated_offsets[4] = -1,                 calibrated distance is: 203 
left2right_top2down_spad_centers[5] = 181, uncalibrated distance is: 177 
calibrated_offsets[5] = 24,                 calibrated distance is: 201 
left2right_top2down_spad_centers[6] = 213, uncalibrated distance is: 179 
calibrated_offsets[6] = 21,                 calibrated distance is: 200 
left2right_top2down_spad_centers[7] = 245, uncalibrated distance is: 210 
calibrated_offsets[7] = -8,                 calibrated distance is: 202 
left2right_top2down_spad_centers[8] = 110, uncalibrated distance is: 203 
calibrated_offsets[8] = 0,                 calibrated distance is: 203 
left2right_top2down_spad_centers[9] = 78, uncalibrated distance is: 174 
calibrated_offsets[9] = 25,                 calibrated distance is: 199 
left2right_top2down_spad_centers[10] = 46, uncalibrated distance is: 175 
calibrated_offsets[10] = 25,                 calibrated distance is: 200 
left2right_top2down_spad_centers[11] = 14, uncalibrated distance is: 209 
calibrated_offsets[11] = -5,                 calibrated distance is: 204 
left2right_top2down_spad_centers[12] = 106, uncalibrated distance is: 221 
calibrated_offsets[12] = -15,                 calibrated distance is: 206 
left2right_top2down_spad_centers[13] = 74, uncalibrated distance is: 199 
calibrated_offsets[13] = 1,                 calibrated distance is: 200 
left2right_top2down_spad_centers[14] = 42, uncalibrated distance is: 200 
calibrated_offsets[14] = 3,                 calibrated distance is: 203 
left2right_top2down_spad_centers[15] = 10, uncalibrated distance is: 227 
calibrated_offsets[15] = -18,                 calibrated distance is: 209

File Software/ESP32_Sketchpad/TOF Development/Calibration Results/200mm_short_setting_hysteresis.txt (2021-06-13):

EEPROM readback data[0]: -24 
EEPROM readback data[1]: -6 
EEPROM readback data[2]: -5 
EEPROM readback data[3]: -27 
EEPROM readback data[4]: -2 
EEPROM readback data[5]: 24 
EEPROM readback data[6]: 22 
EEPROM readback data[7]: -7 
EEPROM readback data[8]: 0 
EEPROM readback data[9]: 27 
EEPROM readback data[10]: 25 
EEPROM readback data[11]: -5 
EEPROM readback data[12]: -15 
EEPROM readback data[13]: 1 
EEPROM readback data[14]: 3 
EEPROM readback data[15]: -17 

---

EEPROM readback data[0]: -24 
EEPROM readback data[1]: -6 
EEPROM readback data[2]: -6 
EEPROM readback data[3]: -25 
EEPROM readback data[4]: -1 
EEPROM readback data[5]: 24 
EEPROM readback data[6]: 22 
EEPROM readback data[7]: -8 
EEPROM readback data[8]: 0 
EEPROM readback data[9]: 27 
EEPROM readback data[10]: 26 
EEPROM readback data[11]: -5 
EEPROM readback data[12]: -15 
EEPROM readback data[13]: 1 
EEPROM readback data[14]: 3 
EEPROM readback data[15]: -18 

VL53L1X is initialized
original width: 16, original height: 16 
original center: 199 
new width: 16, new height: 16 
new center: 199 
Calculating true distances given 200.000000 mm away flat surface 
t:-3, p: -3, L2R_T2B_distances[0] = 206.377975 
t:-3, p: -1, L2R_T2B_distances[1] = 203.516937 
t:-3, p: 1, L2R_T2B_distances[2] = 203.516937 
t:-3, p: 3, L2R_T2B_distances[3] = 206.377975 
t:-1, p: -3, L2R_T2B_distances[4] = 203.516937 
t:-1, p: -1, L2R_T2B_distances[5] = 200.695557 
t:-1, p: 1, L2R_T2B_distances[6] = 200.695557 
t:-1, p: 3, L2R_T2B_distances[7] = 203.516937 
t:1, p: -3, L2R_T2B_distances[8] = 203.516937 
t:1, p: -1, L2R_T2B_distances[9] = 200.695557 
t:1, p: 1, L2R_T2B_distances[10] = 200.695557 
t:1, p: 3, L2R_T2B_distances[11] = 203.516937 
t:3, p: -3, L2R_T2B_distances[12] = 206.377975 
t:3, p: -1, L2R_T2B_distances[13] = 203.516937 
t:3, p: 1, L2R_T2B_distances[14] = 203.516937 
t:3, p: 3, L2R_T2B_distances[15] = 206.377975 
Taking 50 samples of each 16 ROIs to find average reported distance... 
sample: 0 
sample: 1 
sample: 2 
sample: 3 
sample: 4 
sample: 5 
sample: 6 
sample: 7 
sample: 8 
sample: 9 
sample: 10 
sample: 11 
sample: 12 
sample: 13 
sample: 14 
sample: 15 
sample: 16 
sample: 17 
sample: 18 
sample: 19 
sample: 20 
sample: 21 
sample: 22 
sample: 23 
sample: 24 
sample: 25 
sample: 26 
sample: 27 
sample: 28 
sample: 29 
sample: 30 
sample: 31 
sample: 32 
sample: 33 
sample: 34 
sample: 35 
sample: 36 
sample: 37 
sample: 38 
sample: 39 
sample: 40 
sample: 41 
sample: 42 
sample: 43 
sample: 44 
sample: 45 
sample: 46 
sample: 47 
sample: 48 
sample: 49 
find offsets between average and true distances and save in EEPROM... 
spad_avg: 231.000000, real: 206.377975, calibrated_differences[0]: -24.000000 
spad_avg: 209.820038, real: 203.516937, calibrated_differences[1]: -6.000000 
spad_avg: 210.159912, real: 203.516937, calibrated_differences[2]: -6.000000 
spad_avg: 231.459976, real: 206.377975, calibrated_differences[3]: -25.000000 
spad_avg: 205.139984, real: 203.516937, calibrated_differences[4]: -1.000000 
spad_avg: 176.380005, real: 200.695557, calibrated_differences[5]: 24.000000 
spad_avg: 178.039993, real: 200.695557, calibrated_differences[6]: 22.000000 
spad_avg: 211.539963, real: 203.516937, calibrated_differences[7]: -8.000000 
spad_avg: 202.860031, real: 203.516937, calibrated_differences[8]: 0.000000 
spad_avg: 173.639999, real: 200.695557, calibrated_differences[9]: 27.000000 
spad_avg: 174.479980, real: 200.695557, calibrated_differences[10]: 26.000000 
spad_avg: 209.139999, real: 203.516937, calibrated_differences[11]: -5.000000 
spad_avg: 221.660004, real: 206.377975, calibrated_differences[12]: -15.000000 
spad_avg: 202.400009, real: 203.516937, calibrated_differences[13]: 1.000000 
spad_avg: 200.080017, real: 203.516937, calibrated_differences[14]: 3.000000 
spad_avg: 225.160004, real: 206.377975, calibrated_differences[15]: -18.000000 
EEPROM readback data[0]: -24 
EEPROM readback data[1]: -6 
EEPROM readback data[2]: -6 
EEPROM readback data[3]: -25 
EEPROM readback data[4]: -1 
EEPROM readback data[5]: 24 
EEPROM readback data[6]: 22 
EEPROM readback data[7]: -8 
EEPROM readback data[8]: 0 
EEPROM readback data[9]: 27 
EEPROM readback data[10]: 26 
EEPROM readback data[11]: -5 
EEPROM readback data[12]: -15 
EEPROM readback data[13]: 1 
EEPROM readback data[14]: 3 
EEPROM readback data[15]: -18 
left2right_top2down_spad_centers[0] = 145, uncalibrated distance is: 229 
calibrated_offsets[0] = -24,                 calibrated distance is: 205 
left2right_top2down_spad_centers[1] = 177, uncalibrated distance is: 209 
calibrated_offsets[1] = -6,                 calibrated distance is: 203 
left2right_top2down_spad_centers[2] = 209, uncalibrated distance is: 210 
calibrated_offsets[2] = -6,                 calibrated distance is: 204 
left2right_top2down_spad_centers[3] = 241, uncalibrated distance is: 232 
calibrated_offsets[3] = -25,                 calibrated distance is: 207 
left2right_top2down_spad_centers[4] = 149, uncalibrated distance is: 205 
calibrated_offsets[4] = -1,                 calibrated distance is: 204 
left2right_top2down_spad_centers[5] = 181, uncalibrated distance is: 176 
calibrated_offsets[5] = 24,                 calibrated distance is: 200 
left2right_top2down_spad_centers[6] = 213, uncalibrated distance is: 178 
calibrated_offsets[6] = 22,                 calibrated distance is: 200 
left2right_top2down_spad_centers[7] = 245, uncalibrated distance is: 214 
calibrated_offsets[7] = -8,                 calibrated distance is: 206 
left2right_top2down_spad_centers[8] = 110, uncalibrated distance is: 204 
calibrated_offsets[8] = 0,                 calibrated distance is: 204 
left2right_top2down_spad_centers[9] = 78, uncalibrated distance is: 175 
calibrated_offsets[9] = 27,                 calibrated distance is: 202 
left2right_top2down_spad_centers[10] = 46, uncalibrated distance is: 173 
calibrated_offsets[10] = 26,                 calibrated distance is: 199 
left2right_top2down_spad_centers[11] = 14, uncalibrated distance is: 212 
calibrated_offsets[11] = -5,                 calibrated distance is: 207 
left2right_top2down_spad_centers[12] = 106, uncalibrated distance is: 221 
calibrated_offsets[12] = -15,                 calibrated distance is: 206 
left2right_top2down_spad_centers[13] = 74, uncalibrated distance is: 200 
calibrated_offsets[13] = 1,                 calibrated distance is: 201 
left2right_top2down_spad_centers[14] = 42, uncalibrated distance is: 199 
calibrated_offsets[14] = 3,                 calibrated distance is: 202 
left2right_top2down_spad_centers[15] = 10, uncalibrated distance is: 222 
calibrated_offsets[15] = -18,                 calibrated distance is: 204

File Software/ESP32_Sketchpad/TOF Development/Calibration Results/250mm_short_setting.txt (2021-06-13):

EEPROM readback data[0]: -27 
EEPROM readback data[1]: -8 
EEPROM readback data[2]: -7 
EEPROM readback data[3]: -26 
EEPROM readback data[4]: -4 
EEPROM readback data[5]: 19 
EEPROM readback data[6]: 19 
EEPROM readback data[7]: -6 
EEPROM readback data[8]: -1 
EEPROM readback data[9]: 22 
EEPROM readback data[10]: 22 
EEPROM readback data[11]: -4 
EEPROM readback data[12]: -15 
EEPROM readback data[13]: 0 
EEPROM readback data[14]: 3 
EEPROM readback data[15]: -16 

EEPROM readback data[0]: -27 
EEPROM readback data[1]: -8 
EEPROM readback data[2]: -8 
EEPROM readback data[3]: -26 
EEPROM readback data[4]: -4 
EEPROM readback data[5]: 19 
EEPROM readback data[6]: 19 
EEPROM readback data[7]: -6 
EEPROM readback data[8]: -2 
EEPROM readback data[9]: 21 
EEPROM readback data[10]: 22 
EEPROM readback data[11]: -5 
EEPROM readback data[12]: -16 
EEPROM readback data[13]: 0 
EEPROM readback data[14]: 2 
EEPROM readback data[15]: -16 

----

VL53L1X is initialized
original width: 16, original height: 16 
original center: 199 
new width: 16, new height: 16 
new center: 199 
Calculating true distances given 250.000000 mm away flat surface 
t:-3, p: -3, L2R_T2B_distances[0] = 257.972473 
t:-3, p: -1, L2R_T2B_distances[1] = 254.396179 
t:-3, p: 1, L2R_T2B_distances[2] = 254.396179 
t:-3, p: 3, L2R_T2B_distances[3] = 257.972473 
t:-1, p: -3, L2R_T2B_distances[4] = 254.396179 
t:-1, p: -1, L2R_T2B_distances[5] = 250.869461 
t:-1, p: 1, L2R_T2B_distances[6] = 250.869461 
t:-1, p: 3, L2R_T2B_distances[7] = 254.396179 
t:1, p: -3, L2R_T2B_distances[8] = 254.396179 
t:1, p: -1, L2R_T2B_distances[9] = 250.869461 
t:1, p: 1, L2R_T2B_distances[10] = 250.869461 
t:1, p: 3, L2R_T2B_distances[11] = 254.396179 
t:3, p: -3, L2R_T2B_distances[12] = 257.972473 
t:3, p: -1, L2R_T2B_distances[13] = 254.396179 
t:3, p: 1, L2R_T2B_distances[14] = 254.396179 
t:3, p: 3, L2R_T2B_distances[15] = 257.972473 
Taking 50 samples of each 16 ROIs to find average reported distance... 
sample: 0 
sample: 1 
sample: 2 
sample: 3 
sample: 4 
sample: 5 
sample: 6 
sample: 7 
sample: 8 
sample: 9 
sample: 10 
sample: 11 
sample: 12 
sample: 13 
sample: 14 
sample: 15 
sample: 16 
sample: 17 
sample: 18 
sample: 19 
sample: 20 
sample: 21 
sample: 22 
sample: 23 
sample: 24 
sample: 25 
sample: 26 
sample: 27 
sample: 28 
sample: 29 
sample: 30 
sample: 31 
sample: 32 
sample: 33 
sample: 34 
sample: 35 
sample: 36 
sample: 37 
sample: 38 
sample: 39 
sample: 40 
sample: 41 
sample: 42 
sample: 43 
sample: 44 
sample: 45 
sample: 46 
sample: 47 
sample: 48 
sample: 49 
find offsets between average and true distances and save in EEPROM... 
spad_avg: 285.679962, real: 257.972473, calibrated_differences[0]: -27.000000 
spad_avg: 263.179993, real: 254.396179, calibrated_differences[1]: -8.000000 
spad_avg: 263.180023, real: 254.396179, calibrated_differences[2]: -8.000000 
spad_avg: 284.260071, real: 257.972473, calibrated_differences[3]: -26.000000 
spad_avg: 258.859985, real: 254.396179, calibrated_differences[4]: -4.000000 
spad_avg: 231.859970, real: 250.869461, calibrated_differences[5]: 19.000000 
spad_avg: 231.839996, real: 250.869461, calibrated_differences[6]: 19.000000 
spad_avg: 260.979950, real: 254.396179, calibrated_differences[7]: -6.000000 
spad_avg: 256.579956, real: 254.396179, calibrated_differences[8]: -2.000000 
spad_avg: 229.040009, real: 250.869461, calibrated_differences[9]: 21.000000 
spad_avg: 228.699997, real: 250.869461, calibrated_differences[10]: 22.000000 
spad_avg: 259.420013, real: 254.396179, calibrated_differences[11]: -5.000000 
spad_avg: 274.059937, real: 257.972473, calibrated_differences[12]: -16.000000 
spad_avg: 254.300018, real: 254.396179, calibrated_differences[13]: 0.000000 
spad_avg: 251.500000, real: 254.396179, calibrated_differences[14]: 2.000000 
spad_avg: 274.659973, real: 257.972473, calibrated_differences[15]: -16.000000 
EEPROM readback data[0]: -27 
EEPROM readback data[1]: -8 
EEPROM readback data[2]: -8 
EEPROM readback data[3]: -26 
EEPROM readback data[4]: -4 
EEPROM readback data[5]: 19 
EEPROM readback data[6]: 19 
EEPROM readback data[7]: -6 
EEPROM readback data[8]: -2 
EEPROM readback data[9]: 21 
EEPROM readback data[10]: 22 
EEPROM readback data[11]: -5 
EEPROM readback data[12]: -16 
EEPROM readback data[13]: 0 
EEPROM readback data[14]: 2 
EEPROM readback data[15]: -16 
left2right_top2down_spad_centers[0] = 145, uncalibrated distance is: 288 
calibrated_offsets[0] = -27,                 calibrated distance is: 261 
left2right_top2down_spad_centers[1] = 177, uncalibrated distance is: 264 
calibrated_offsets[1] = -8,                 calibrated distance is: 256 
left2right_top2down_spad_centers[2] = 209, uncalibrated distance is: 265 
calibrated_offsets[2] = -8,                 calibrated distance is: 257 
left2right_top2down_spad_centers[3] = 241, uncalibrated distance is: 281 
calibrated_offsets[3] = -26,                 calibrated distance is: 255 
left2right_top2down_spad_centers[4] = 149, uncalibrated distance is: 257 
calibrated_offsets[4] = -4,                 calibrated distance is: 253 
left2right_top2down_spad_centers[5] = 181, uncalibrated distance is: 230 
calibrated_offsets[5] = 19,                 calibrated distance is: 249 
left2right_top2down_spad_centers[6] = 213, uncalibrated distance is: 231 
calibrated_offsets[6] = 19,                 calibrated distance is: 250 
left2right_top2down_spad_centers[7] = 245, uncalibrated distance is: 263 
calibrated_offsets[7] = -6,                 calibrated distance is: 257 
left2right_top2down_spad_centers[8] = 110, uncalibrated distance is: 259 
calibrated_offsets[8] = -2,                 calibrated distance is: 257 
left2right_top2down_spad_centers[9] = 78, uncalibrated distance is: 225 
calibrated_offsets[9] = 21,                 calibrated distance is: 246 
left2right_top2down_spad_centers[10] = 46, uncalibrated distance is: 227 
calibrated_offsets[10] = 22,                 calibrated distance is: 249 
left2right_top2down_spad_centers[11] = 14, uncalibrated distance is: 257 
calibrated_offsets[11] = -5,                 calibrated distance is: 252 
left2right_top2down_spad_centers[12] = 106, uncalibrated distance is: 276 
calibrated_offsets[12] = -16,                 calibrated distance is: 260 
left2right_top2down_spad_centers[13] = 74, uncalibrated distance is: 256 
calibrated_offsets[13] = 0,                 calibrated distance is: 256 
left2right_top2down_spad_centers[14] = 42, uncalibrated distance is: 257 
calibrated_offsets[14] = 2,                 calibrated distance is: 259 
left2right_top2down_spad_centers[15] = 10, uncalibrated distance is: 277 
calibrated_offsets[15] = -16,                 calibrated distance is: 261

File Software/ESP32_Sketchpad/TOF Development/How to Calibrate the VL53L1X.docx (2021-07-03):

Step 1:

Tape the sides of the Shelly unit to a piece of light paper, such that the VL53L1X sensor is sitting just above the edge of the paper. The edge of the paper will be used to measure the distance between the sensor and the wall.

Step 2:

Tape the paper 1cm away from the edge of a heavy, dark and flat hardcover book. This book will provide stability to ensure the sensor doesn’t move during the calibration. By taping the paper 1cm away from the edge of the book cover, a contrast is created that can be used to easily spot the location of the paper’s edge.

Step 3:

Print out a paper with a solid grey colour covering its surface. The colour should be Munsell N9.5, or in RGB values: Red = 244, Green = 243, Blue = 239. You can use Microsoft Paint to create this RGB colour.

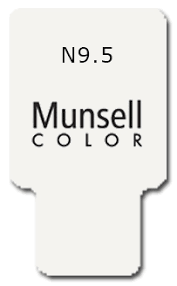
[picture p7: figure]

Step 4:

Tape the grey coloured paper to a vertical wall.

Step 5:

Place the textbook that is taped to the VL53L1X sensor about 14cm away from the grey paper on the wall. The VL53L1X sensor should be pointing roughly at the center of the paper. Use other hardcover books to reach this position

Step 6:

Connect the Micro USB cable from the Shelly unit to the computer.

Step 7:

With a rectangular stiff ruler, and compensating for any non-marked edge space on the ruler, position both the left and right edges of the paper (which the sensor is taped to) to be exactly 14mm away from the grey vertical wall paper. This measurement should be done when the edge of the ruler is flush the face of the wall to ensure the VL53L1X sensor is not angled away from the wall. See the images below for an example.

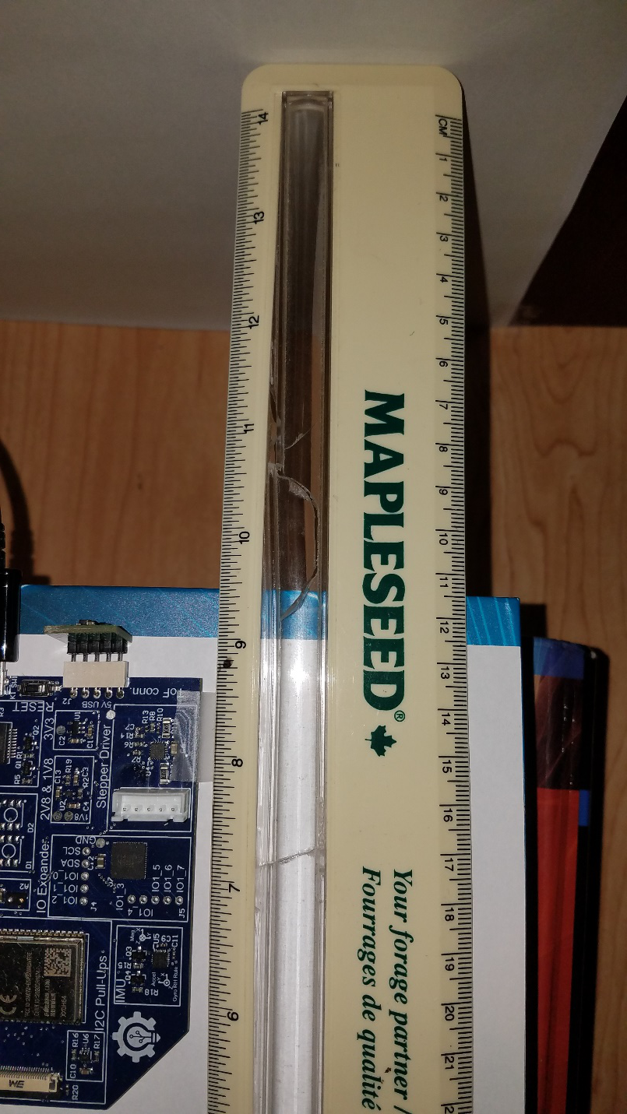
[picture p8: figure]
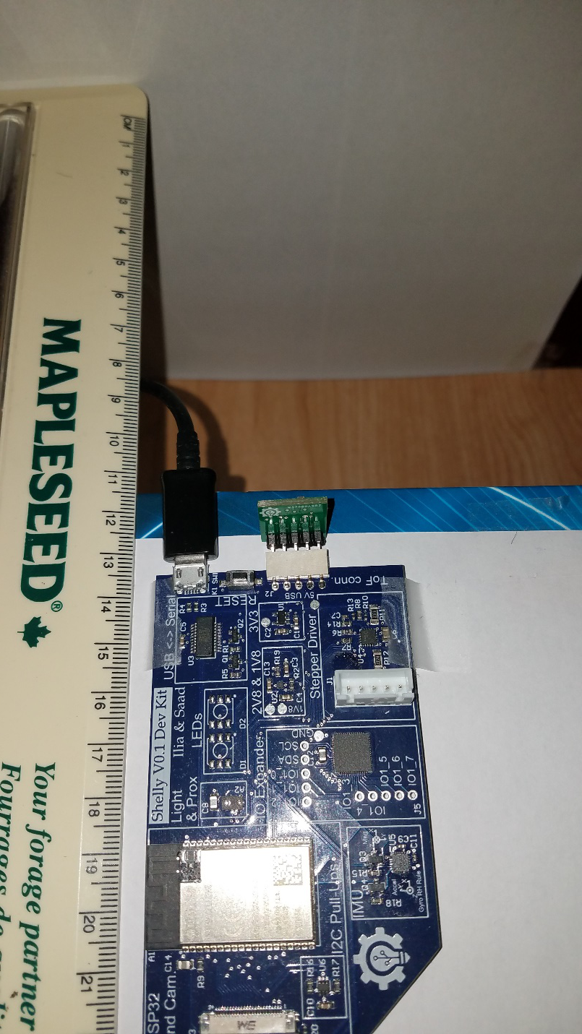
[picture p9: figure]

Step 8:

Open “Calibration_Attemp1.ino” Arduino file.

Step 9:

Edit the Calibration_Attemp1.ino code such that the variable “flat_distance” on line 405 within the “calibrate_allspads()” function is set to “140.0”. See the image below for an example.

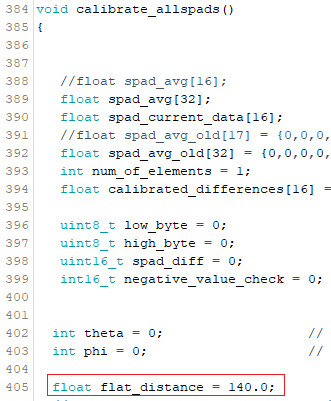
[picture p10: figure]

Step 10:

Install and run the code in ”Calibration_Attemp1.ino” in the shelly unit. This code will calculate the exact theoretical vector distance from each SPAD to the wall, then average the readings for 16 4x4 SPADs on the VL53L1X sensor, then save the differences (offsets) between the measured and theoretical distance for each SPAD in the ESP32 EEPROM.

Step 11:

Install the non-calibration application firmware for the Shelly unit. Use the function “void retrieve_EEPROM_data(int16_t *data_array_pointer)” defined in “Calibration_Attemp1.ino” to retrieve the SPAD offsets and correct for distance measurements. See below for an example:

int16_t calibrated_offsets[16];

retrieve_EEPROM_data(calibrated_offsets);

for(int i2 = 0; i2 < 16; i2++ ) // for each of the 16 SPADS SPAD

{

sensor.setROISize(4, 4);

sensor.setROICenter(left2right_top2down_spad_centers[i2]); // uint8_t left2right_top2down_spad_centers[16] = {145, 177, 209, 241, 149, 181, 213, 245, 110, 78, 46, 14, 106, 74, 42, 10};

// get the reading for that SPAD

sensor.readSingle(false); // start single measurement

while (!sensor.dataReady())

{

//wait for sensor data

}

distance_in_millimeters = (uint32_t)(((int16_t)sensor.read(false)) + calibrated_offsets[i2]);

}

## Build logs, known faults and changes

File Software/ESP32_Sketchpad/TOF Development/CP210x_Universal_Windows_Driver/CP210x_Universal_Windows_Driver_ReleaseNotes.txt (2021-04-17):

RELEASE NOTES
=============
Silicon Labs Virtual COM Port (VCP) Universal Driver for Windows 10

Package version: 10.1.10
Release date:    2021-01-13

This package contains a Virtual COM Port Universal driver for Microsoft
Windows 10 for use with Silicon Labs VCP USB Serial Bridges.  These devices
include the CP2102N, CP2102, CP2103, CP2104, CP2105, CP2108, CP2109.

OS VERSIONS
-----------
This package provides the CP210x VCP driver for the following versions
of Windows:

- Windows 10    (x64, x86)

CHOOSING VCP DRIVER VERSION
---------------------------
VCP drivers of version 10.0.0 and later are released for Windows 10 as
Universal Drivers.  This means they do not work on older version of Windows
such as Window 7 and 8.1.  You should use this driver if you only need
support for Windows 10, or you need the Universal driver.  If you require
support on older versions of Windows, you should use the legacy VCP driver
which can be found on the Silicon Labs web site.  The legacy Windows VCP
drivers have version numbers less than 10.0.0.

CONTENTS
--------
The VCP driver package contains the following files and directories:
- silabser.inf -- Driver information file
- CP210xVCPInstaller_x64.exe -- 64-bit installer
- CP210xVCPInstaller_x86.exe -- 32-bit installer
- SLAB_License_Agreement_VCP_Windows.txt -- Software License
- CP210x_Universal_Windows_Driver_ReleaseNotes.txt -- this file

Additional files needed by installer
- dpinst.xml
- silabser.cat
- x64/silabser.sys
- x86/silabser.sys

INSTALLING
----------
The VCP driver is automatically installed by Windows Update for CP210x with
alternate PID values of 0xEA63, 0xEA7A, and 0xEA7B.  These are not default
values.

Otherwise, unzip the .zip file and you will have a directory containing the
driver installer files.

### Prompted install ###

If Windows prompts you to install a driver for a CP210x device
(for example, if you plug a CP210x into your computer):

1. Use the dialog to browse for the driver location
2. Locate the driver folder (that you previously unzipped)
3. Follow the instructions

### Manual install ###

1. Using Windows File Explorer, locate the driver folder
   (that you previously unzipped)
2. Determine if you have 32-bit or 64-bit Windows
3. Double click to run the .exe file named CP210xVCPInstaller_xnn.exe
   (where xnn is x64 for 64-bit and x86 is for 32-bit)
4. Follow the instructions

UNINSTALLING
------------
1. The device must be plugged in
2. Run Device Manager
3. Locate the device you want to uninstall
4. Right click on the device and choose "uninstall"
5. Follow the instructions

SUPPORT
-------
For technical support please visit the Silicon Labs support site:

https://www.silabs.com/support

******************************************************************************
    RELEASE NOTES FOR 10.1.10 (2021-01-13)

Changes for VCP Driver
==============================================================================
MCUSW-651    | Support baud rate up to 2187500 for CP2102, CP2104, CP2109
MCUSW-685    | Fixed the Blue Screen issue when running Windows Hardware Lab   
             | Kit for customized driver                                       
MCUSW-783    | Microsoft Windows Certified (aka "WHQL Certified") for Windows  
             | 10 version 20H2 (2020-10-20)                                    

******************************************************************************
    RELEASE NOTES FOR 10.1.9 (2020-07-30)

Changes for VCP Driver
==============================================================================
MCUSW-566    | Remove sanity/error checking on IOCTL_SERIAL_SET_BAUD_RATE for  
             | CP2103 devices.                                                 
MCUSW-596    | Microsoft Windows Certified (aka "WHQL Certified") for Windows  
             | 10 version 2004 (2020-05-27)                                    
MCUSW-619    | Support for Directed PoFx (DFx - Directed Power Management      
             | Framework).                                                     

******************************************************************************
    RELEASE NOTES FOR 10.1.8 (2019-06-24 (DriverVer = 06/20/2019,10.1.8.2466))

Changes for VCP Driver
==============================================================================
MCUSW-412    | Certified for Windows 10 RS6.                                   
MCUSW-484    | WDFVERIFY() added to the driver. Configurable via Registry.    
MCUSW-493    | Improved the tagging/tracking and parent-hierarchy of framework
             | objects and framework object reference counts. 
MCUSW-495    | Clear RTS on CloseHandle().                                     
MCUSW-508    | IOCTL_SERIAL_GET_COMMSTATUS refactored to reduce USB-bus        
             | bandwidth, while still offering timely reporting.               
MCUSW-518    | WDFVerifier parameter ForceLogsInMiniDump Registry parameter    
             | added for improved supportability.                              
MCUSW-519    | Resolve an SDV-identified issue: do not double-complete a       
             | Request on error paths.                                         
MCUSW-526    | Creates the framework USB device object with client contract    
             | version USBD_CLIENT_CONTRACT_VERSION_602/0x602 (I.e. Register   
             | with "new" (to Windows 8) Windows USB driver stack).            

******************************************************************************
    RELEASE NOTES FOR 10.1.7 (2019-03-26 (DriverVer = 03/26/2019,10.1.7.2399))

Changes for VCP Driver
==============================================================================
MCUSW-473    | Fix length of nul-terminated legacy Dos Name string written to  
             | HARDWARE\DEVICEMAP\SERIALCOMM Registry key.                     
MCUSW-483    | Fixed bug for Max Baud rate for CP2101, CP2104, CP2105 and
             | CP2108 devices.                                                        

******************************************************************************
    RELEASE NOTES FOR 10.1.6 (2019-03-19 (DriverVer = 03/15/2019,10.1.6.2388))

Changes for VCP Driver
==============================================================================
MCUSW-445    | Fix a blue-screen system crash bug with handling of ioctl       
             | IOCTL_SERIAL_WAIT_ON_MASK during power state changes.           

******************************************************************************
    RELEASE NOTES FOR 10.1.5 (2019-02-19 (DriverVer = 02/19/2019,10.1.5.2368))

Changes for VCP Driver
==============================================================================
MCUSW-414    | Implement an undocumented Registry-configured feature to ignore 
             | IOCTL_SERIAL_PURGE.                                             
MCUSW-417    | Read many of the Registry "parameter"-type settings first from  
             | the "parameters key" and then from the "hardware key", with the 
             | "hardware key" taking precedence (allows "driver wide, all      
             | devices" setting, but provides the capability to specify per-   
             | device settings (before we only supported per-device            
             | settings)).                                                     
             |                                                                 
MCUSW-439    | Fixed a bug whereby Close()-Open() on a CP2102N could get USB   
             | data toggle confused (I.e. issue USB CLEAR_FEATURE(HALT) to     
             | bulk endpoints to reset data toggle back to DATA0).             
MCUSW-449    | Fix a Max Baud Rate bug (use device-specific MaxBauds (from the 
             | data-sheets): 3 Mbaud for CP2102N, 1 Mbaud for all other CP210x 
             | devices.).                                                      
MCUSW-450    | Fix Verification BSOD (race condition in the VCP device driver  
             | that can cause double completions): Only call                   
             | DetachForCompletionUNcancelable on success of UNmark as         
             | cancelable in handling of IOCTL_SERIAL_WAIT_ON_MASK-related     
             | requests.                                                       

******************************************************************************
    RELEASE NOTES FOR 10.1.4 (2018-12-07 (DriverVer = 11/26/2018,10.1.4.2290))

Changes for VCP Driver
==============================================================================
MCUSW-134    | Fixed an issue with handling of IOCTL_SERIAL_SET_WAIT_MASK,     
             | IOCTL_SERIAL_WAIT_ON_MASK, with the SERIAL_EV_RXCHAR event and  
             | data arriving from the device into the driver. Previously, an   
             | indication of arriving data was made before making the data     
             | available, causing, in some conditions, subsequent requests for 
             | data after notification of data available to not deliver any    
             | data.                                                           
MCUSW-144    | Onecore-based editions of Windows 10 (I.e. Windows 10 IoT Core) 
             | do not, by design, create PortName entries in the Registry to   
             | specify the device's legacy DOS name (I.e. COM<n).              
             | Consequently, VCP enhanced to not treat this as a failing       
             | condition and to continue without creating legacy COM<n> DOS    
             | devices.                                                        
MCUSW-148    | Rearchitected into two VCP driver packages:                     
             |  1) Windows 7 and later Desktop Editions x86 and x64 driver     
             | package, and                                                    
             |  2) Windows Universal (10 and later; Desktop, tablet, mobile,   
             | embedded) x86, x64, ARM, ARM64 driver package.                  
MCUSW-214    | Windows 10 Universal driver release (I.e. no Windows 7, 8 or    
             | 8.1 support)                                                    
MCUSW-352    | Workaround to issue where close during receipt of serial data   
             | caused CP2102N to hang.                                         
MCUSW-369    | Certified for Windows 10 RS5.                                   
MCUSW-393    | Fix bug due to some BaudRate-related math causing a divide-by-  
             | zero.                                                           
MCUSW-396    | Be defensive against the impossible case of getting a NULL      
             | object in the object completion routine.                        

******************************************************************************
    RELEASE NOTES FOR 10.1.3 (2018-05-29)

Changes for VCP Driver
==============================================================================
MCUSW-326    | Clear DTR on CloseHandle().                                     

******************************************************************************
    RELEASE NOTES FOR 10.1.2 (2018-05-14)

Changes for VCP Driver
==============================================================================
MCUSW-134    | Fixed an issue with handling of IOCTL_SERIAL_SET_WAIT_MASK,     
             | IOCTL_SERIAL_WAIT_ON_MASK, with the SERIAL_EV_RXCHAR event and  
             | data arriving from the device into the driver. Previously, an   
             | indication of arriving data was made before making the data     
             | available, causing, in some conditions, subsequent requests for 
             | data after notification of data available to not deliver any    
             | data.                                                           
MCUSW-211    | Windows 10 Universal driver release (I.e. no Windows 7, 8 or    
             | 8.1 support)                                                    
MCUSW-288    | Fix IOCTL_SERIAL_GET_PROPERTIES.                                
MCUSW-291    | Fix IOCTL_SERIAL_GET_PROPERTIES/SERIAL_COMMPROP for CP210x-like 
             | "Voice MB v2.0" device.                                         
MCUSW-315    | Certified for RS4/1803.                                         

******************************************************************************
    RELEASE NOTES FOR 10.1.1 (DriverVer=11/15/2017,10.1.1.1951)

Changes for VCP Driver
==============================================================================
MCUSW-134    | Fixed an issue with handling of IOCTL_SERIAL_SET_WAIT_MASK,
             | IOCTL_SERIAL_WAIT_ON_MASK, with the SERIAL_EV_RXCHAR event
             | and data arriving from the device into the driver. Previously,
             | an indication of arriving data was made before making the data
             | available, causing, in some conditions, subsequent requests
             | for data after notification of data available to not deliver
             | any data. 

******************************************************************************
LEGACY HISTORY
--------------
Everything below is the shared development history before creation of the
Windows 10 Universal driver.  Everything above is development history of
the Universal driver.

******************************************************************************
    RELEASE NOTES FOR 6.7.5 (2017-10-13)

Changes for VCP Driver
==============================================================================
MCUSW-17     | IOCTL_SERIAL_GET_STATUS TransmittedCount fixed.                 
MCUSW-19     | CP210x_GET_CONFIG_DESCRIPTOR_IOCTL returned byte count fixed.   
MCUSW-21     | Revert IOCTL_SERIAL_GET_COMMSTATUS behaviour to return cached   
             | information (reverse slowdown reported with v6.7.4 in some      
             | applications)                                                   
             |                                                                 
             | Improve windbg logging, w.r.t. doing less when logging is not   
             | enabled (say, Release builds), or when particular subsystem is  
             | not enabled for logging.                                        
             |                                                                 
MCUSW-110    | Windows 10 certified against RS2 (Creators Update).             
MCUSW-207    | In a failed initialization, discard a reference to dynamically  
             | allocated memory once memory has been freed.                    
MCUSW-234    | timestamp SHA2 Signatures with SHA2 timestamps                  

******************************************************************************
    RELEASE NOTES FOR 6.7.4.261 (2017/01/30)

- Device Guard compliant
- CP210XFW-747: Add 3 new parallel PIDs one each for the single-, dual- &
  quad-port CP210x devices (to be distributed via Windows Update)
- CP210XFW-741: Fix driver to use correct interface string index for the
  multi-interface CP210x devices (CP2105 & CP2108). Return iProduct string
  for other CP210x devices.
- CP210XFW-713: Add protection against IRP_MJ_CLOSE coming before
  IRP_MJ_CLEANUP. In such case EvtFileCleanup callback was called with 0
  FileObject, causeing a crash. Serenum is suspected of causing this, even
  though there is no proof except that it's present, was introduced recently
  and this crash was never registered before.
- CP210XFW-691: Fixed race between timer activation and request cancelation
  during processing of read rwquests.
- Changed raw WDF read request timer to our wrapper.
- CP210XFW-693: bugfix: WMI command "wmic path Win32_SerialPort get
  Availability^, DeviceID^, Name" is unable to enumerate the port.
- CP210XFW-686: EvtRequestCancel for wait mask IRP crashed because the
  request was already completed. It didn't serialize well with other places
  that can complete it. It looked like XOff IRP may have the same proble. This
  patch is adding an extra check into *all* other EvtRequestCancel functions
  to make sure this doesn't happen again.
- Changed IOCTLs returning polled-cached MDMSTS to explicitly read the
  status. Use reg value DisableHwAccessInModemStatusIoctls to revert this
  new functionality to old behavior.
- Improved debug prints.
- SerialDbgPrintEx used 1K of stack for the string, reduced to 256.
- Resolved many static Code Analysis warnings
- Added accounting for data in chip's TX queue. Added translation of
  COMM_STATUS::ulErrors into SERIAL_EV_BREAK and SERIAL_EV_ERR.
- CP210XFW-549, CP210XFW-536, CP210XFW-546: Generate events for
  IOCTL_SERIAL_SET_WAIT_MASK from COMM_STATUS::ulErrors. Can be disabled by
  DisableCommStatusPolling reg value.
- Added spinlock around ModemStatus change detection. Refactored modem
  status event signalling to use common function.
- Move passive level functions into the paged section.
- MCUFW-740: Made device close operation wait for chip's Tx queue to empty.
  Added registry settings DisableTxEmptyCheckInClose and
  TxEmptyTimeoutOnCloseInMs.
- Improve control transfer debug prints and clean up code, otherwise no
  functional changes.
- MCUFW-740: Fixed EV_TXEMPTY to account for bytes in chip's Tx queue.
- MCUFW-740: New functions to sync access to comm error storage from
  multiple threads.
- Added DisableTxEmptyCheckInGetCommStatusIoctl reg value.
- Refactor control request I/O. MCUFW-740: Fixed
  IOCTL_SERIAL_GET_COMMSTATUS.
- MCUFW-740: Made device close operation wait for chip's Tx queue to empty.
  Added registry settings DisableTxEmptyCheckInClose and
  TxEmptyTimeoutOnCloseInMs.
- CP210XFW-648: Set a three second timeout on
  WdfUsbTargetDeviceSendControlTransferSynchronously().

******************************************************************************
    RELEASE NOTES FOR 6.7.3 (2016/03/03)

- Down-rev the verison of KMDF the driver uses (CP210XFW-591. Use version of
  KMDF natively included on Windows release)
- Bug fix of blue-screen system crash (CP210XFW-575. driver tries to clear a
  Cancel Routine in a Request that doesn't have it.)

******************************************************************************
    RELEASE NOTES FOR 6.7.2 (2015/11/23)

- Unified Windows 7, 8, 8.1 & 10 support (XP, Vista and Server 2003
  available in version 6.7).
- ARM support added for Windows 10 and Windows 10 IoT Core.
- Silicon Labs-specific Serial Enumeration driver silabenm removed in favor
  of the Windows "in-box" serenm.
- UpperFilter Serial Enumeration driver not enabled by default
- Updated to latest Microsoft build tools
- Resolved /W4 compilation warnings
- Resolved code analysis warnings
- Added a registry value ControlHandShakeForcedSetBits that can force
  certain bits in the ControlHandShake variable to always be set.
- Add SAL-annotations to API header files.
- Bugfix an invalid memory access on device stop.
- Standardize branding Properties resources across all deliverables.
- Digitally sign all signable deliverables.
- Rewrote driver synchronization for data transmission paths.
- Resolve bugs arising from extended stress test.
- Added diagnostic variables to device extension.
- Bugfix a Write IRP stuck forever cauding bugcheck 9f-4 if call to USB
  returns with error.
- Bugfix "packetized write" timeout may fail to act. And improved debug
  prints.
- New reg value DisableS0Idle (default: 0) to replace EnablePowerManagewment
  (default: 0 which actually ment "enable"). Also, DisableS0Idle=1 now
  forces AllowIdleWhileOpen to 0.
- Driver ignores BreakOnEntry, DebugLevel and DebugFlag in registry.
- New CP2108 bug workarounds - GET_LINE_CTL byte swap and tx_empty().
- Fixed crash in read path.
- Simplified, commented and synchronized with NEWSTUFF EvtIoStop and
  EvtIoResume.
- Fixed memory leak on device removal when multiple devices are present.
- Bugfix Read IRP may never complete if other read IRPs are already waiting
  when it arrives.
- Add CP2102N part numbers. Hnadle new part numbers in
  WriteLatch()/ReadLatch().
- Resolve HCK INF warnings that became errors on HLK.
- Bugfix: Potential invalid memory access on device stop.
- Fixed possible memory overrun when writing CP2108 latch.
- Cumulative collection of improvements (due to code analysis, application
  of latest toolset, etc.) and bug fixes.

******************************************************************************
    RELEASE NOTES FOR 6.7.1 (2015/06/29)

- Added certification for Windows 10 Preview (Note: Windows 10 only;
  use v6.7 for Windows prior to Windows 10)

******************************************************************************
    RELEASE NOTES FOR 6.7 (2014/04/11)

- Added vendor-specific commands to the driver that do not affect normal
  operation with standard CP210x devices.
- Modified write behavior to packetize data as a work around for a rare
  USB 2.0 hub behavior seen only in Windows XP (x86).

******************************************************************************
    RELEASE NOTES FOR 6.6.1 (2013/10/24)

- Added certification for Windows 8.1
- Added support for CP2108 devices
- Corrected bug where OS would hang on repetition of many rapid open/closes on
  certain systems.

******************************************************************************
    RELEASE NOTES FOR 6.6

- Moving installer format to DPInst
- Supported under Windows 8
- Corrected bug in total write timeout calculation
- Corrected bug where EV_BREAK event could be misreported based on incoming
  data
- Corrected another BSOD corner case regarding write cancellation

******************************************************************************
    RELEASE NOTES FOR 6.5.3

- Corrected BSOD corner case for a write cancellation
- Corrected memory leak that occurs when a device is plugged/unplugged
  rapidly enough to allow driver startup function to fail

******************************************************************************
    RELEASE NOTES FOR 6.5

- Corrected BSOD corner case issue for handling control requests
- Corrected issue where USB 3.0 hubs would deliver data to the driver out
  of order

******************************************************************************
    RELEASE NOTES FOR 6.4

- Corrected multiple BSOD issues by updating request handling for control
  requests to the USB device, and the write completion method
- Corrected device removal routine to also undo the COM port naming in the
  registry at removal time instead of when the device is closed after the
  removal.

******************************************************************************
    RELEASE NOTES FOR 6.3a

- Updated to 3.2 DriverInstaller to correct a bug seen when updating from an
  old driver installer version	

******************************************************************************
    RELEASE NOTES FOR 6.3

- Corrected a bug introduced in 6.2 which caused BSOD during surprise removal.
- Corrected a bug found in I/O cancellation corner case

******************************************************************************
    RELEASE NOTES FOR 6.2

- Corrected return value for DeviceIoControl() and other COM API functions
  once the device is removed to properly show ERROR_ACCESS_DENIED (0x05)
  instead of ERROR_BAD_COMMAND in GetLastError()
- Corrected bug in DTR/RTS reporting latency seen if you set DTR/RTS and ask
  for it before the device has reported it to the host - now when it is
  written it reads back immediately
- Corrected several USB requests that were improperly defined as device
  requests when they are actually interface requests - this doesn't exhibit
  and bugs in current single interface devices but was changed to be complete
  and correct
- Added support for CP2104 and CP2105 devices	

******************************************************************************
    RELEASE NOTES FOR 6.1

- Corrected a memory leak which could bog the system down after extended use
  of a contiuously opened COM port, and conditionally yield bluescreens on
  certain systems
- Corrected a problem where an IO reqest would sometimes return a busy
  status to user mode, instead the queue is restarted if necessary before
  adding an IO request to the queue
- Corrected a condition which would blue screen on cancelling write request
  that hasn't been fully sent out USB
- Corrected the Capabilites return value, which incorrectly reported that
  timeouts are not supported
- Corrected several Queue size return values, which affected behavior in the
  MSCOMM control
- Corrected DTR/RTS value on device insertion, visible when Serial
  Enumeration is disabled
- Corrected the ability to override Baud Rate and Line Control from the INF
  file

******************************************************************************
    RELEASE NOTES FOR 6.0

- Corrected multiple blue screens and driver hangs related to race
  conditions in the driver
- Corrected problem where driver hangs when 4 or more devices are connected
  to a single transaction translator hub
- Corrected bugs that prohibited serial enumeration
- Corrected problem where IO requests were not completed/cancelled on a
  close
- Corrected problem with dialing out or PPP connections
- Created IO queueing mechanism so that multiple reads, writes, etc. can be
  queued and waited on

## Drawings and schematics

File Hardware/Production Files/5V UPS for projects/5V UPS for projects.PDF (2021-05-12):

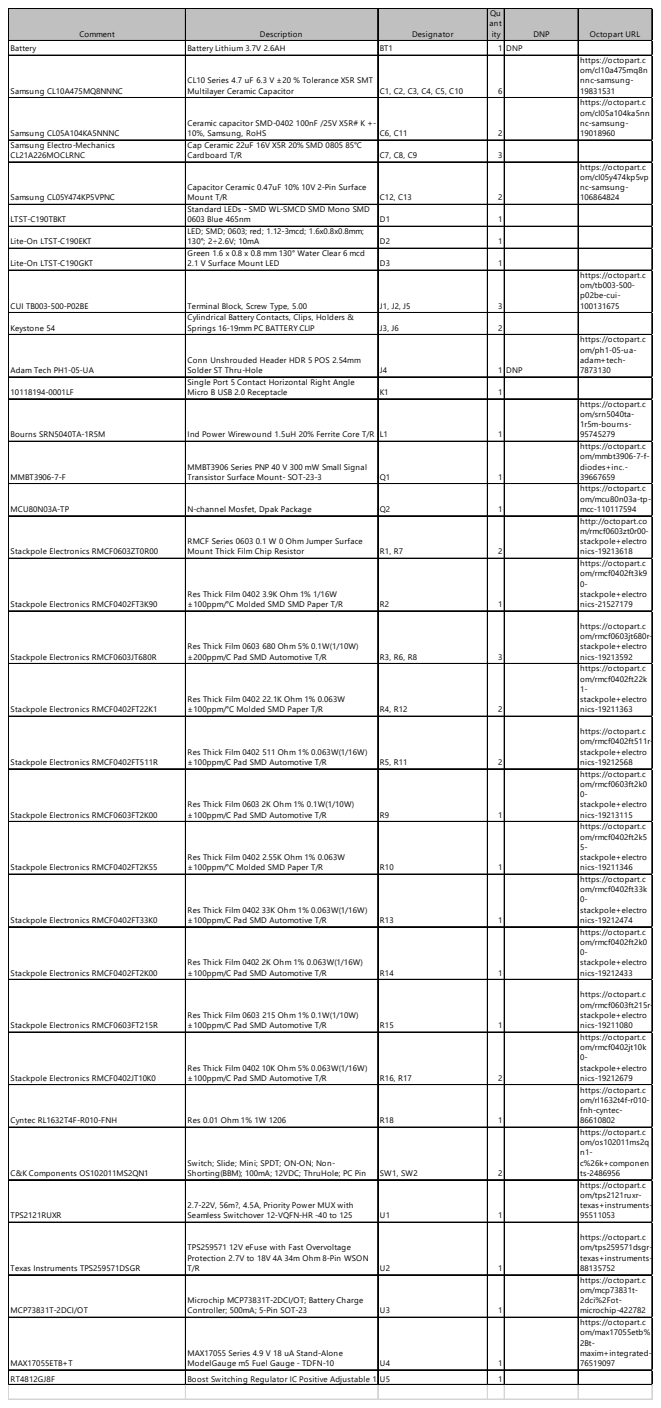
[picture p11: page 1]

Comment | Description | Designator | Qu ant ity | DNP | Octopart URL

Battery | Battery Lithium 3.7V 2.6AH | BT1 | 1 | DNP
Samsung CL10A475MQ8NNNC | CL10 Series 4.7 uF 6.3 V ±20 % Tolerance X5R SMT Multilayer Ceramic Capacitor | C1, C2, C3, C4, C5, C10 | 6 | | https://octopart.com/cl10a475mq8n nnc-samsung-19831531

Samsung CL05A104KA5NNNC | Ceramic capacitor SMD-0402 100nF /25V X5R# K +-10%, Samsung, RoHS | C6, C11 | 2 | | https://octopart.com/cl05a104ka5nn nc-samsung-19018960

Samsung Electro-Mechanics CL21A226MOCLRNC | Cap Ceramic 22uF 16V X5R 20% SMD 0805 85°C Cardboard T/R | C7, C8, C9 | 3

Samsung CL05Y474KP5VPNC | Capacitor Ceramic 0.47uF 10% 10V 2-Pin Surface Mount T/R | C12, C13 | 2 | | https://octopart.com/cl05y474kp5vp nc-samsung-106864824

LTST-C190TBKT | Standard LEDs - SMD WL-SMCD SMD Mono SMD 0603 Blue 465nm | D1 | 1

Lite-On LTST-C190EKT | LED; SMD; 0603; red; 1.12-3mcd; 1.6x0.8x0.8mm; 130°; 2÷2.6V; 10mA | D2 | 1

Lite-On LTST-C190GKT | Green 1.6 x 0.8 x 0.8 mm 130° Water Clear 6 mcd 2.1 V Surface Mount LED | D3 | 1

CUI TB003-500-P02BE | Terminal Block, Screw Type, 5.00 | J1, J2, J5 | 3 | | https://octopart.com/tb003-500-p02be-cui-100131675

Keystone 54 | Cylindrical Battery Contacts, Clips, Holders & Springs 16-19mm PC BATTERY CLIP | J3, J6 | 2

Adam Tech PH1-05-UA | Conn Unshrouded Header HDR 5 POS 2.54mm Solder ST Thru-Hole | J4 | 1 | DNP | https://octopart.com/ph1-05-ua-adam+tech-7873130

10118194-0001LF | Single Port 5 Contact Horizontal Right Angle Micro B USB 2.0 Receptacle | K1 | 1

Bourns SRN5040TA-1R5M | Ind Power Wirewound 1.5uH 20% Ferrite Core T/R | L1 | 1 | | https://octopart.com/srn5040ta-1r5m-bourns-95745279

MMBT3906-7-F | MMBT3906 Series PNP 40 V 300 mW Small Signal Transistor Surface Mount- SOT-23-3 | Q1 | 1 | | https://octopart.com/mmbt3906-7-f-diodes+inc.-39667659

MCU80N03A-TP | N-channel Mosfet, Dpak Package | Q2 | 1 | | https://octopart.com/mcu80n03a-tp-mcc-110117594

Stackpole Electronics RMCF0603ZT0R00 | RMCF Series 0603 0.1 W 0 Ohm Jumper Surface Mount Thick Film Chip Resistor | R1, R7 | 2 | | http://octopart.com/rmcf0603zt0r00-stackpole+electro nics-19213618

Stackpole Electronics RMCF0402FT3K90 | Res Thick Film 0402 3.9K Ohm 1% 1/16W ±100ppm/°C Molded SMD SMD Paper T/R | R2 | 1 | | https://octopart.com/rmcf0402ft3k9 0-stackpole+electro nics-21527179

Stackpole Electronics RMCF0603JT680R | Res Thick Film 0603 680 Ohm 5% 0.1W(1/10W) ±200ppm/C Pad SMD Automotive T/R | R3, R6, R8 | 3 | | https://octopart.com/rmcf0603jt680r-stackpole+electro nics-19213592

Stackpole Electronics RMCF0402FT22K1 | Res Thick Film 0402 22.1K Ohm 1% 0.063W ±100ppm/°C Molded SMD Paper T/R | R4, R12 | 2 | | https://octopart.com/rmcf0402ft22k 1-stackpole+electro nics-19211363

Stackpole Electronics RMCF0402FT511R | Res Thick Film 0402 511 Ohm 1% 0.063W(1/16W) ±100ppm/C Pad SMD Automotive T/R | R5, R11 | 2 | | https://octopart.com/rmcf0402ft511r-stackpole+electro nics-19212568

Stackpole Electronics RMCF0603FT2K00 | Res Thick Film 0603 2K Ohm 1% 0.1W(1/10W) ±100ppm/C Pad SMD Automotive T/R | R9 | 1 | | https://octopart.com/rmcf0603ft2k0 0-stackpole+electro nics-19213115

Stackpole Electronics RMCF0402FT2K55 | Res Thick Film 0402 2.55K Ohm 1% 0.063W ±100ppm/°C Molded SMD Paper T/R | R10 | 1 | | https://octopart.com/rmcf0402ft2k5 5-stackpole+electro nics-19211346

Stackpole Electronics RMCF0402FT33K0 | Res Thick Film 0402 33K Ohm 1% 0.063W(1/16W) ±100ppm/C Pad SMD Automotive T/R | R13 | 1 | | https://octopart.com/rmcf0402ft33k 0-stackpole+electro nics-19212474

Stackpole Electronics RMCF0402FT2K00 | Res Thick Film 0402 2K Ohm 1% 0.063W(1/16W) ±100ppm/C Pad SMD Automotive T/R | R14 | 1 | | https://octopart.com/rmcf0402ft2k0 0-stackpole+electro nics-19212433

Stackpole Electronics RMCF0603FT215R | Res Thick Film 0603 215 Ohm 1% 0.1W(1/10W) ±100ppm/C Pad SMD Automotive T/R | R15 | 1 | | https://octopart.com/rmcf0603ft215r-stackpole+electro nics-19211080

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

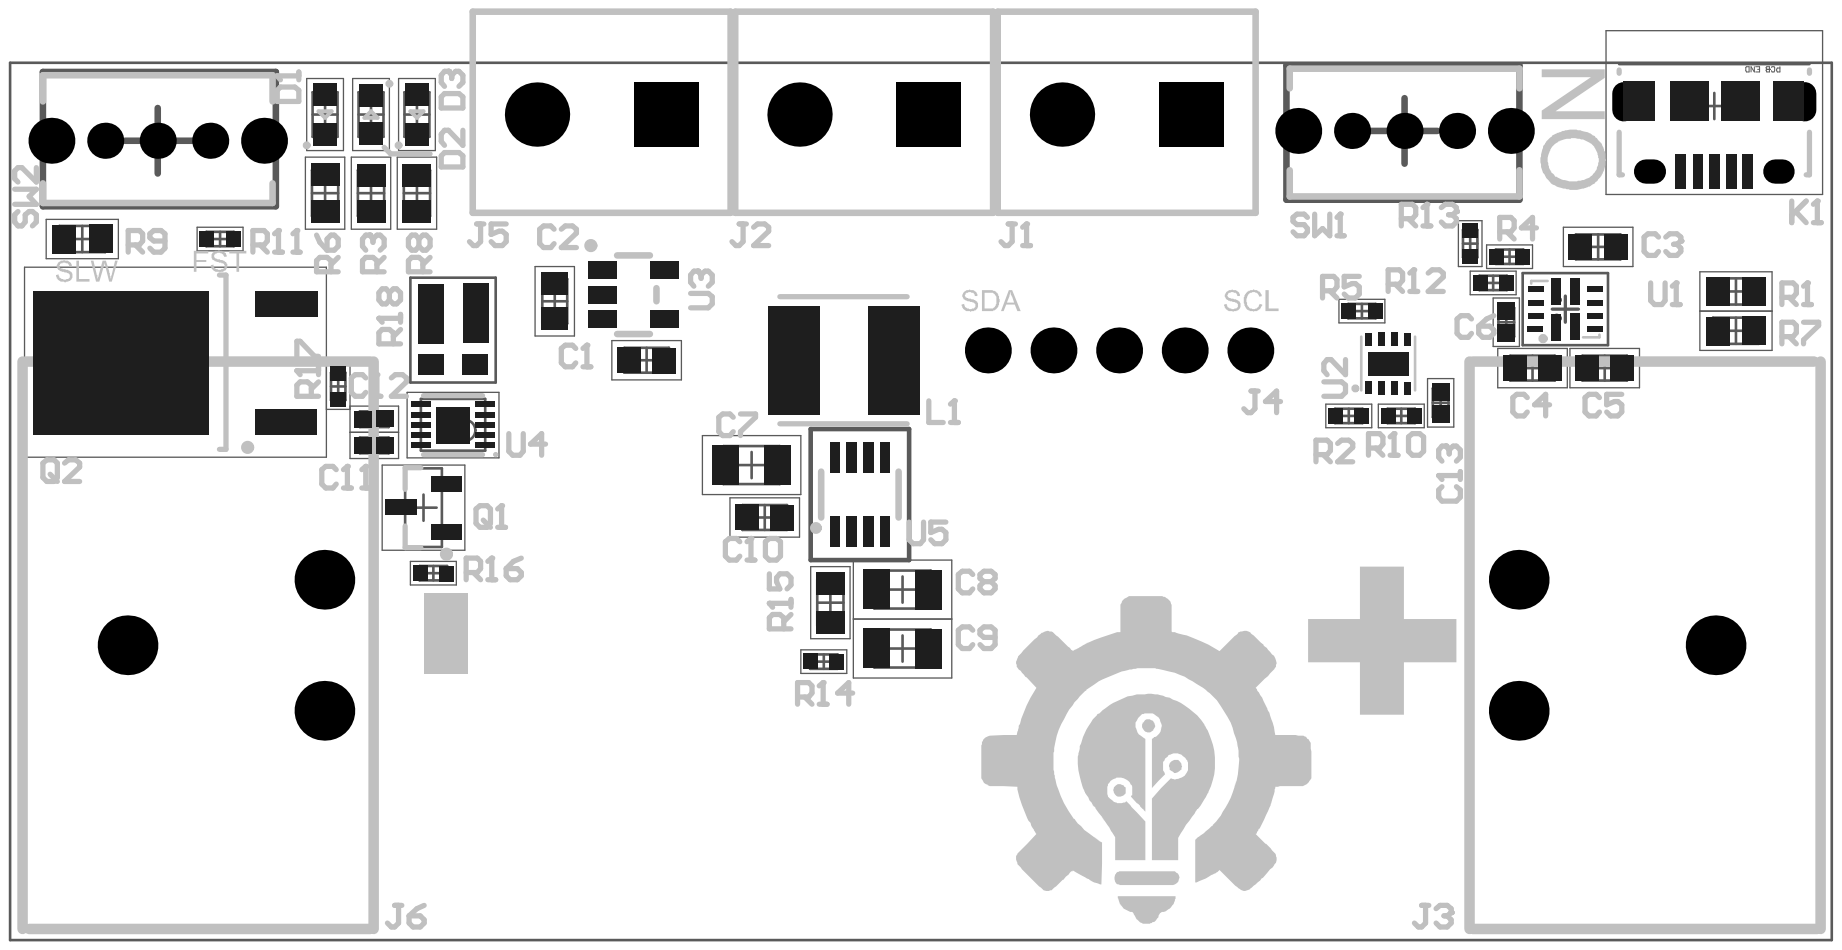
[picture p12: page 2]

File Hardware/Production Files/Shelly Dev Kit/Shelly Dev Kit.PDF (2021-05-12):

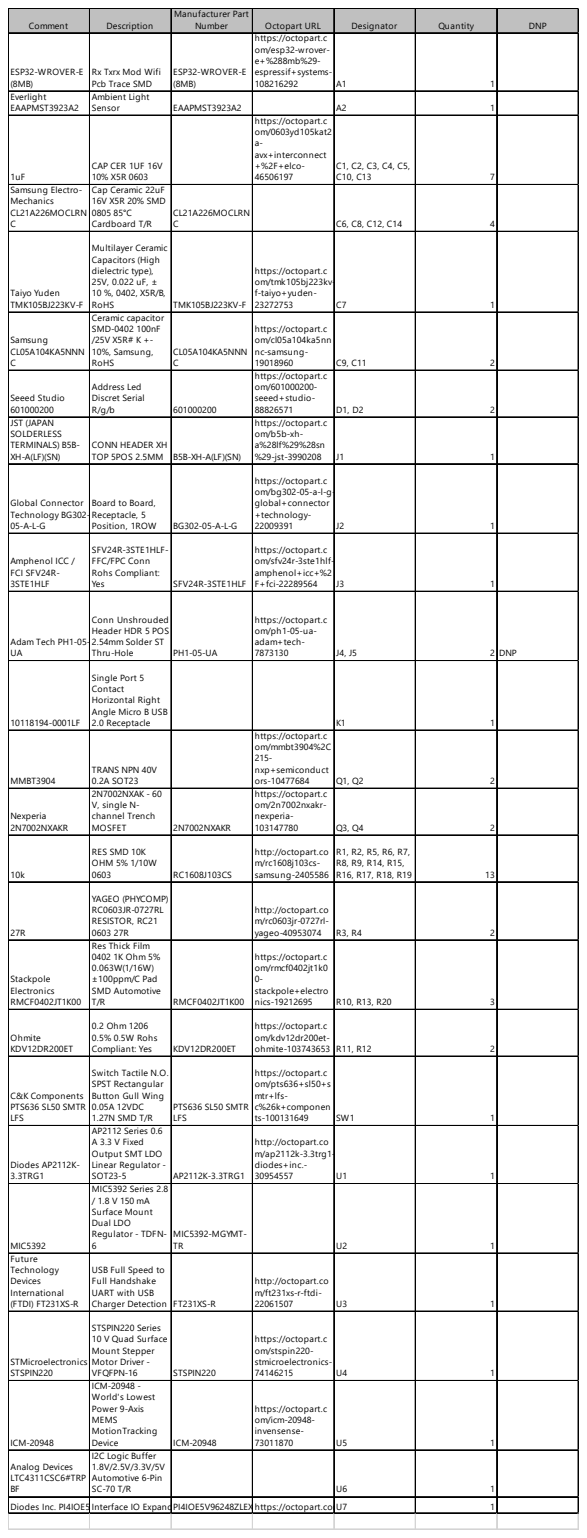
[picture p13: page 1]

Comment | Description | Manufacturer Part Number | Octopart URL | Designator | Quantity | DNP

ESP32-WROVER-E (8MB) | Rx Txrx Mod Wifi Pcb Trace SMD | ESP32-WROVER-E (8MB) | https://octopart.com/esp32-wrover-e+%288mb%29-espressif+systems-108216292 | A1 | 1

Everlight EAAPMST3923A2 | Ambient Light Sensor | EAAPMST3923A2 | | A2 | 1

1uF | CAP CER 1UF 16V 10% X5R 0603 | | https://octopart.com/0603yd105kat2 a-avx+interconnect +%2F+elco-46506197 | C1, C2, C3, C4, C5, C10, C13 | 7

Samsung Electro-Mechanics CL21A226MOCLRN C | Cap Ceramic 22uF 16V X5R 20% SMD 0805 85°C Cardboard T/R | CL21A226MOCLRN C | | C6, C8, C12, C14 | 4

Taiyo Yuden TMK105BJ223KV-F | Multilayer Ceramic Capacitors (High dielectric type), 25V, 0.022 uF, ± 10 %, 0402, X5R/B, RoHS | TMK105BJ223KV-F | https://octopart.com/tmk105bj223kv-f-taiyo+yuden-23272753 | C7 | 1

Samsung CL05A104KA5NNN C | Ceramic capacitor SMD-0402 100nF /25V X5R# K +-10%, Samsung, RoHS | CL05A104KA5NNN C | https://octopart.com/cl05a104ka5nn nc-samsung-19018960 | C9, C11 | 2

Seeed Studio 601000200 | Address Led Discret Serial R/g/b | 601000200 | https://octopart.com/601000200-seeed+studio-88826571 | D1, D2 | 2

JST (JAPAN SOLDERLESS TERMINALS) B5B-XH-A(LF)(SN) | CONN HEADER XH TOP 5POS 2.5MM | B5B-XH-A(LF)(SN) | https://octopart.com/b5b-xh-a%28lf%29%28sn %29-jst-3990208 | J1 | 1

Global Connector Technology BG302-05-A-L-G | Board to Board, Receptacle, 5 Position, 1ROW | BG302-05-A-L-G | https://octopart.com/bg302-05-a-l-g-global+connector +technology-22009391 | J2 | 1

Amphenol ICC / FCI SFV24R-3STE1HLF | SFV24R-3STE1HLF-FFC/FPC Conn Rohs Compliant: Yes | SFV24R-3STE1HLF | https://octopart.com/sfv24r-3ste1hlf-amphenol+icc+%2 F+fci-22289564 | J3 | 1

Adam Tech PH1-05-UA | Conn Unshrouded Header HDR 5 POS 2.54mm Solder ST Thru-Hole | PH1-05-UA | https://octopart.com/ph1-05-ua-adam+tech-7873130 | J4, J5 | 2 | DNP

10118194-0001LF | Single Port 5 Contact Horizontal Right Angle Micro B USB 2.0 Receptacle | | | K1 | 1

MMBT3904 | TRANS NPN 40V 0.2A SOT23 | | https://octopart.com/mmbt3904%2C 215-nxp+semiconduct ors-10477684 | Q1, Q2 | 2

Nexperia 2N7002NXAKR | 2N7002NXAK - 60 V, single N-channel Trench MOSFET | 2N7002NXAKR | https://octopart.com/2n7002nxakr-nexperia-103147780 | Q3, Q4 | 2

10k | RES SMD 10K OHM 5% 1/10W 0603 | RC1608J103CS | http://octopart.com/rc1608j103cs-samsung-2405586 | R1, R2, R5, R6, R7, R8, R9, R14, R15, R16, R17, R18, R19 | 13

27R | YAGEO (PHYCOMP) RC0603JR-0727RL RESISTOR, RC21 0603 27R | | http://octopart.com/rc0603jr-0727rl-yageo-40953074 | R3, R4 | 2

Stackpole Electronics RMCF0402JT1K00 | Res Thick Film 0402 1K Ohm 5% 0.063W(1/16W) ±100ppm/C Pad SMD Automotive T/R | RMCF0402JT1K00 | https://octopart.com/rmcf0402jt1k0 0-stackpole+electro nics-19212695 | R10, R13, R20 | 3

Ohmite KDV12DR200ET | 0.2 Ohm 1206 0.5% 0.5W Rohs Compliant: Yes | KDV12DR200ET | https://octopart.com/kdv12dr200et-ohmite-103743653 | R11, R12 | 2

C&K Components PTS636 SL50 SMTR LFS | Switch Tactile N.O. SPST Rectangular Button Gull Wing 0.05A 12VDC 1.27N SMD T/R | PTS636 SL50 SMTR LFS | https://octopart.com/pts636+sl50+s mtr+lfs-c%26k+componen ts-100131649 | SW1 | 1

Diodes AP2112K-3.3TRG1 | AP2112 Series 0.6 A 3.3 V Fixed Output SMT LDO Linear Regulator -SOT23-5 | AP2112K-3.3TRG1 | http://octopart.com/ap2112k-3.3trg1-diodes+inc.-30954557 | U1 | 1

MIC5392 | MIC5392 Series 2.8 / 1.8 V 150 mA Surface Mount Dual LDO Regulator - TDFN-6 | MIC5392-MGYMT-TR | | U2 | 1

Future Technology Devices International (FTDI) FT231XS-R | USB Full Speed to Full Handshake UART with USB Charger Detection | FT231XS-R | http://octopart.com/ft231xs-r-ftdi-22061507 | U3 | 1

STMicroelectronics STSPIN220 | STSPIN220 Series 10 V Quad Surface Mount Stepper Motor Driver -VFQFPN-16 | STSPIN220 | https://octopart.com/stspin220-stmicroelectronics-74146215 | U4 | 1

ICM-20948 | ICM-20948 -World's Lowest Power 9-Axis MEMS MotionTracking Device | ICM-20948 | https://octopart.com/icm-20948-invensense-73011870 | U5 | 1

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

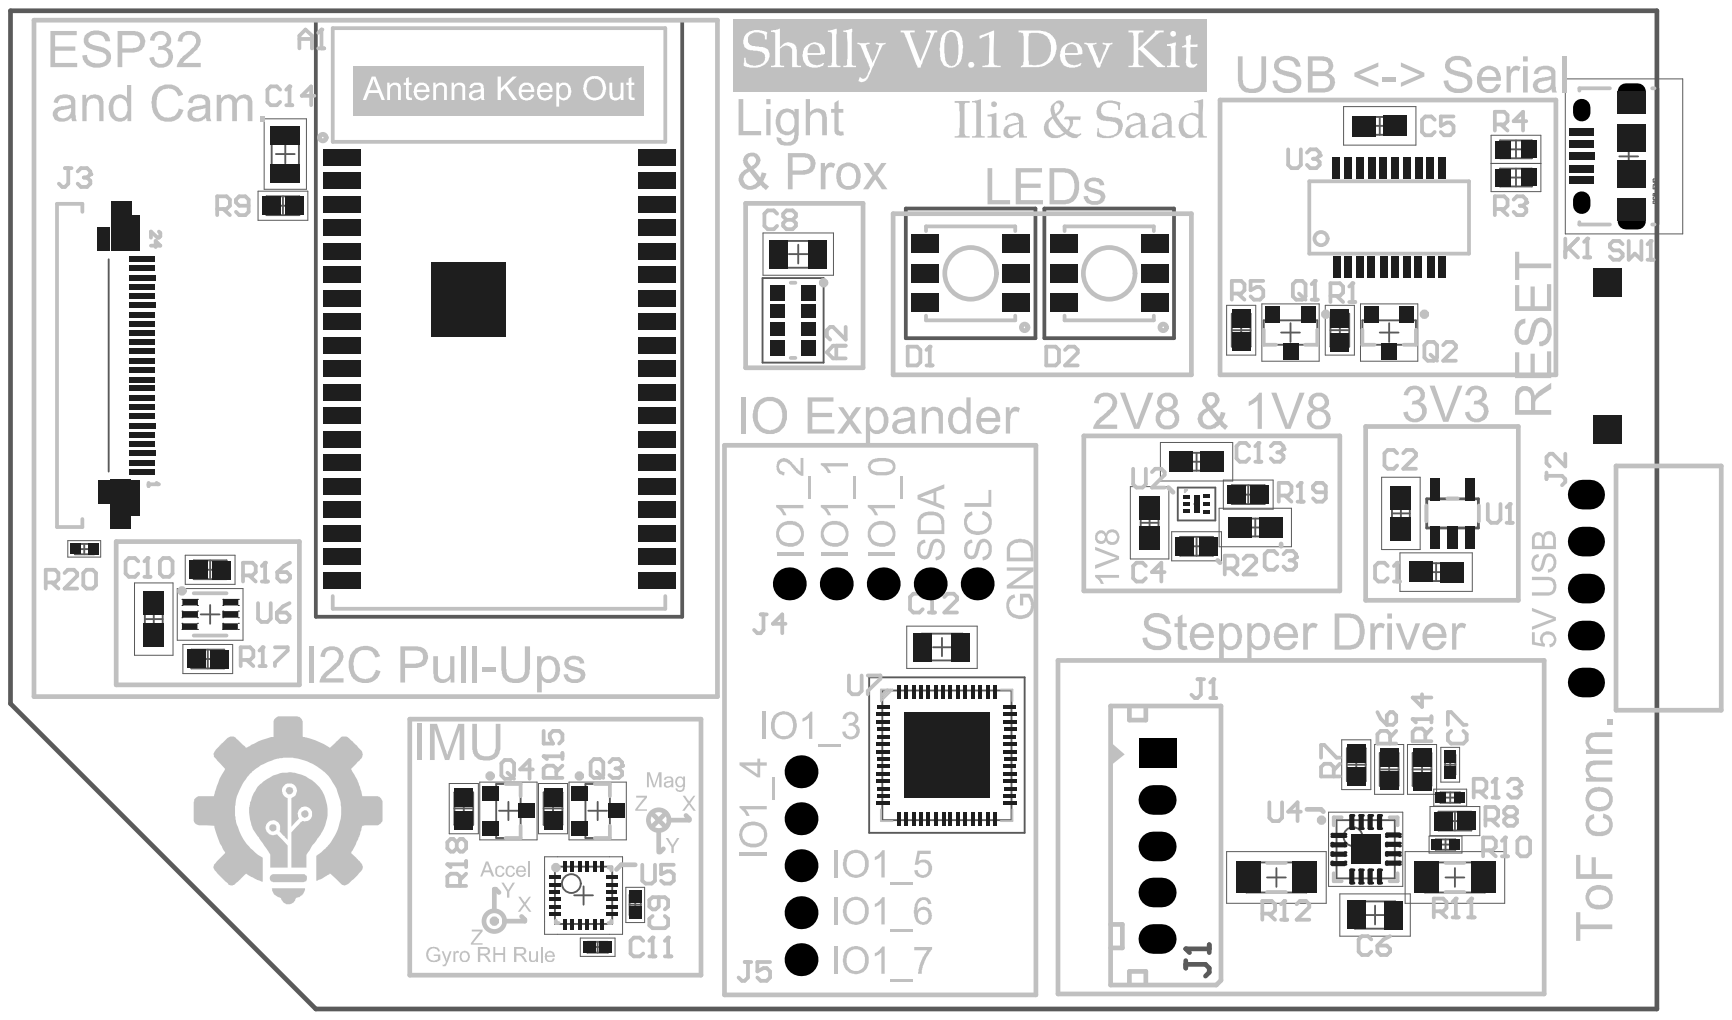
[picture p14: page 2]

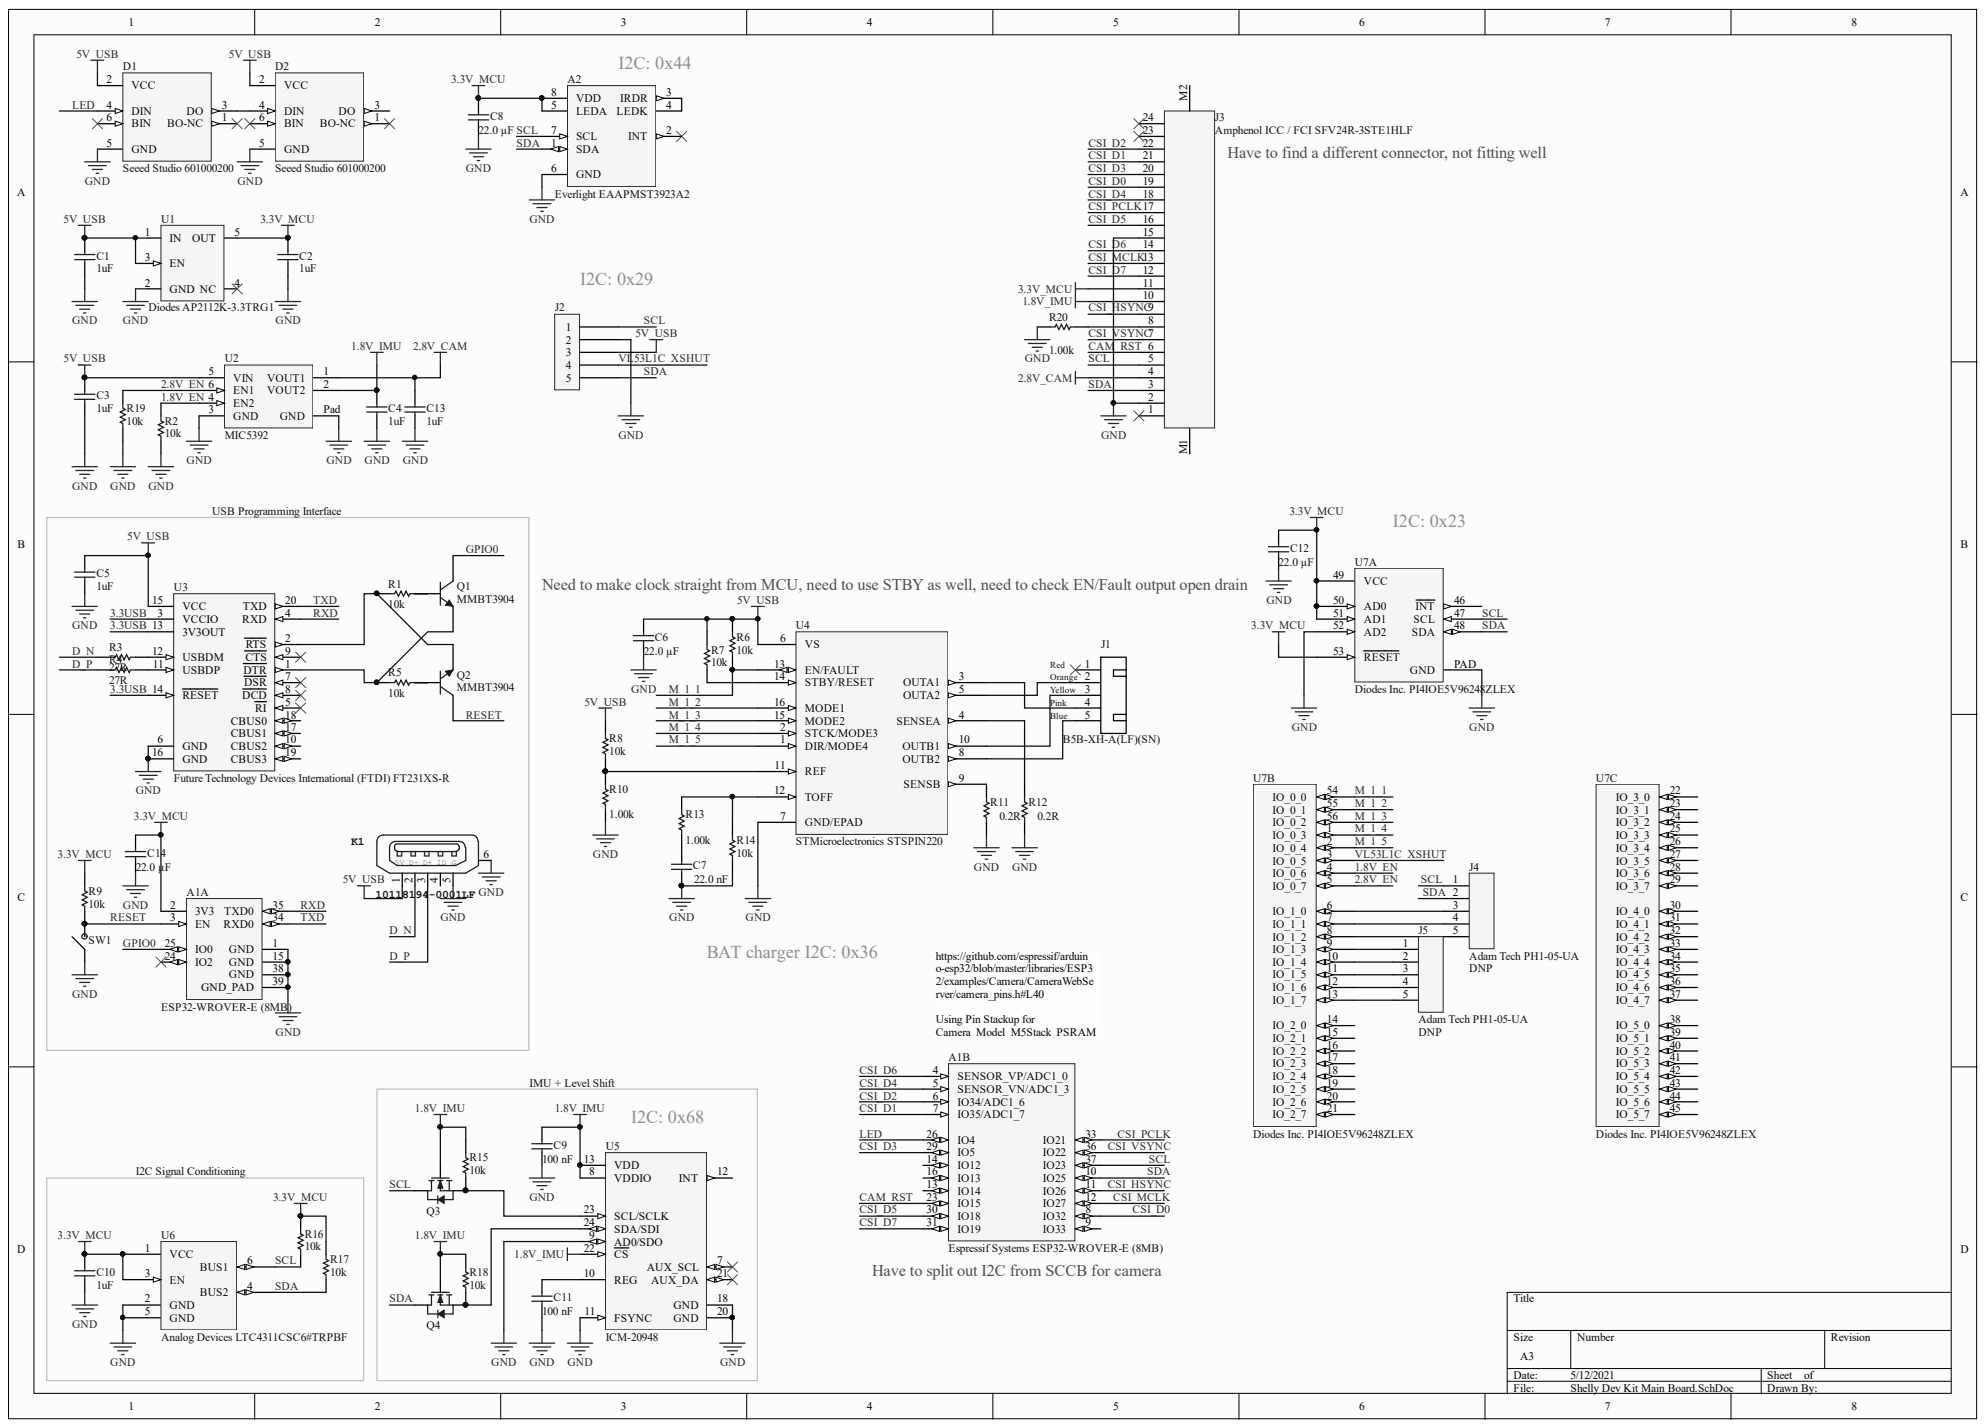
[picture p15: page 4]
Need t; o make cl; ock s; l, need t; o check E; pen drai; charger I2C: 0x36Have t; Have t; g wel

1 0
S Y | N C

2 . 8 V _E N 6 | 2
1 . 8 V _E N 4 | P a d

ht from MCU, need t

se STBY as wel

ut I2C from SCCB for camera

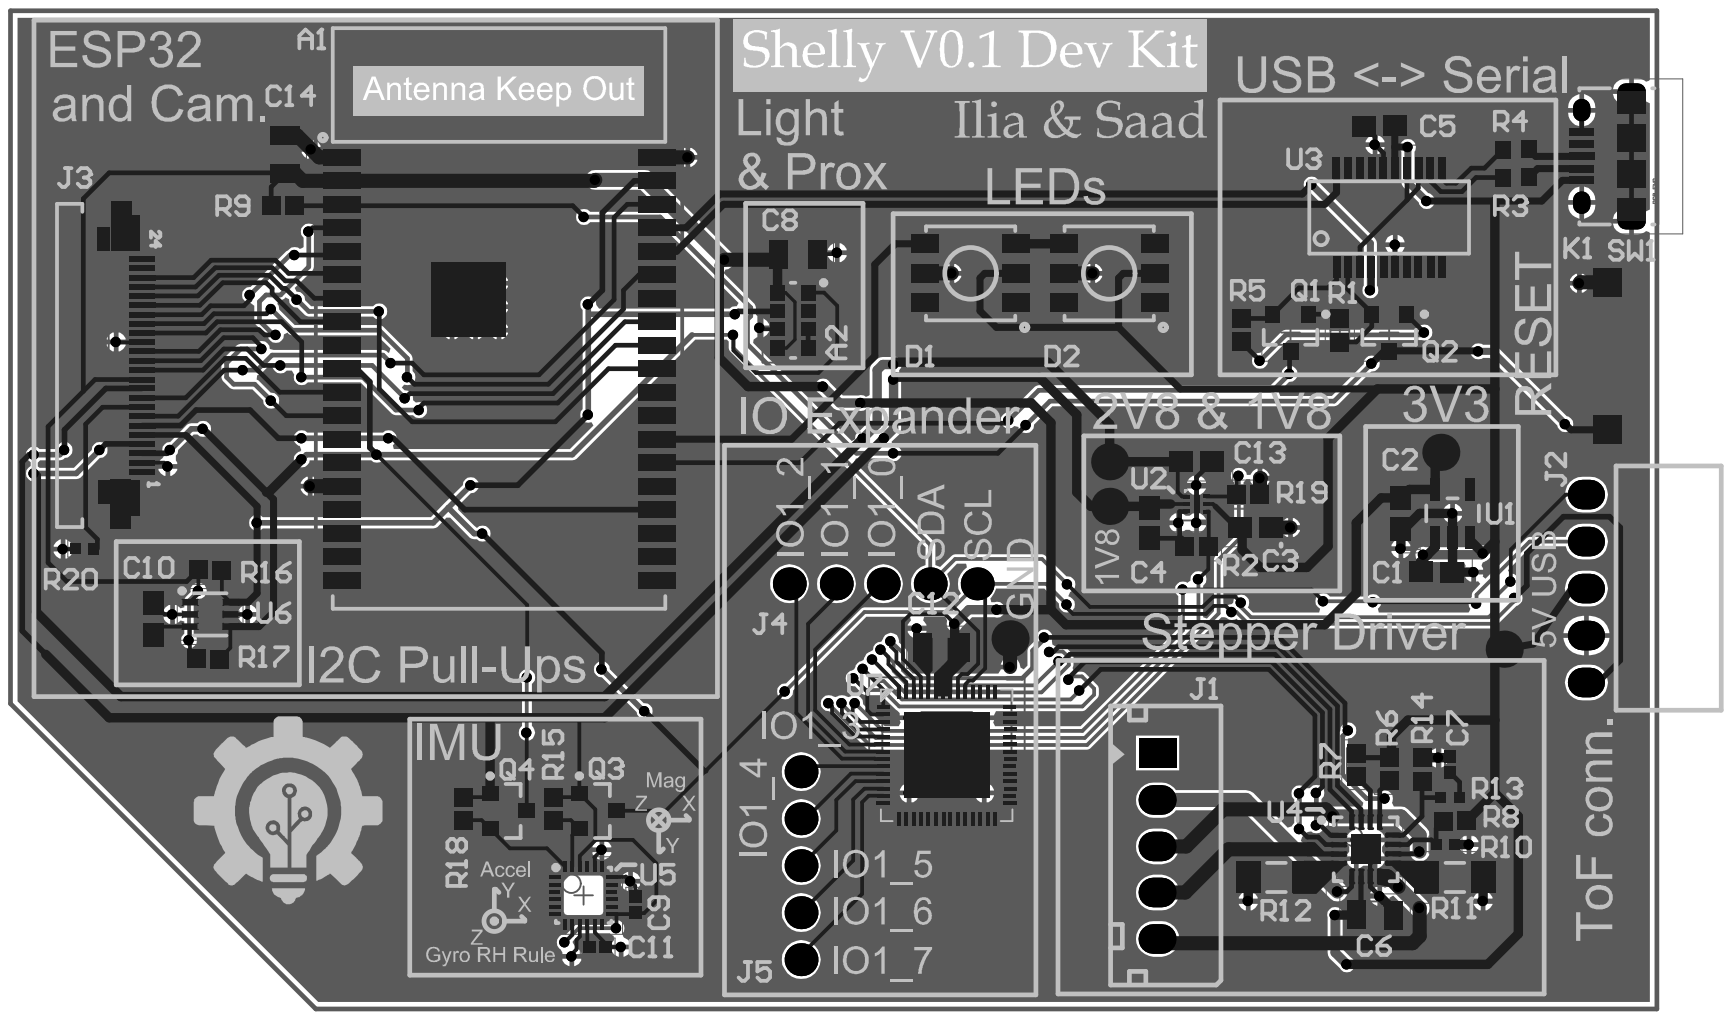
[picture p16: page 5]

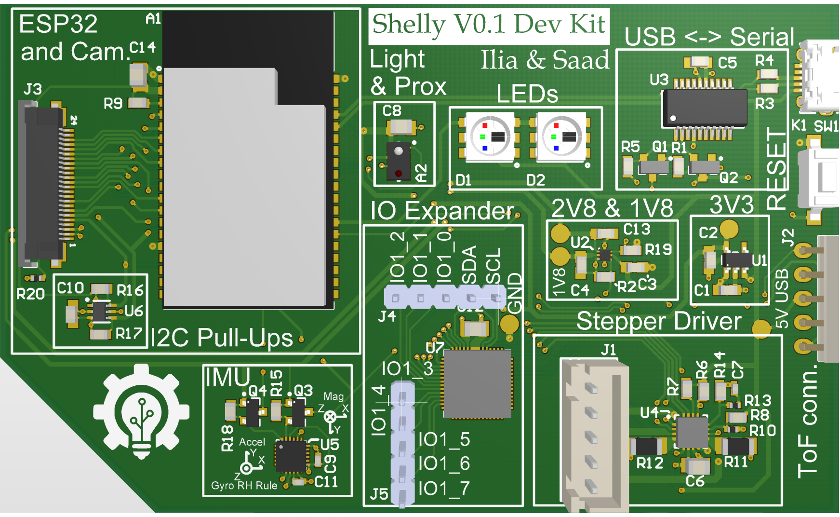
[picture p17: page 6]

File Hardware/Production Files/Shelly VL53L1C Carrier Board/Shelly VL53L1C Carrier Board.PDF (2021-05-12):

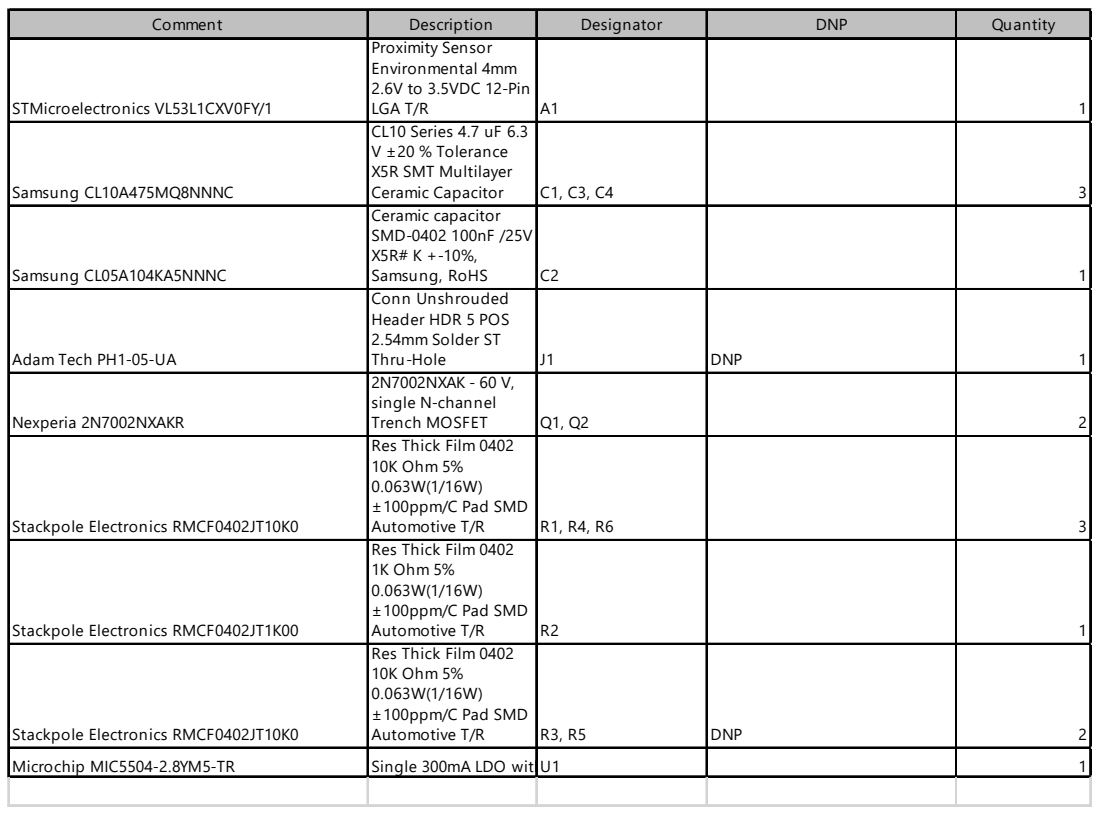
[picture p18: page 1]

Comment | Description | Designator | DNP | Quantity

STMicroelectronics VL53L1CXV0FY/1 | Proximity Sensor Environmental 4mm 2.6V to 3.5VDC 12-Pin LGA T/R | A1 | | 1

Samsung CL10A475MQ8NNNC | CL10 Series 4.7 uF 6.3 V ±20 % Tolerance X5R SMT Multilayer Ceramic Capacitor | C1, C3, C4 | | 3

Samsung CL05A104KA5NNNC | Ceramic capacitor SMD-0402 100nF /25V X5R# K +-10%, Samsung, RoHS | C2 | | 1

Adam Tech PH1-05-UA | Conn Unshrouded Header HDR 5 POS 2.54mm Solder ST Thru-Hole | J1 | DNP | 1

Nexperia 2N7002NXAKR | 2N7002NXAK - 60 V, single N-channel Trench MOSFET | Q1, Q2 | | 2

Stackpole Electronics RMCF0402JT10K0 | Res Thick Film 0402 10K Ohm 5% 0.063W(1/16W) ±100ppm/C Pad SMD Automotive T/R | R1, R4, R6 | | 3

Stackpole Electronics RMCF0402JT1K00 | Res Thick Film 0402 1K Ohm 5% 0.063W(1/16W) ±100ppm/C Pad SMD Automotive T/R | R2 | | 1

Stackpole Electronics RMCF0402JT10K0 | Res Thick Film 0402 10K Ohm 5% 0.063W(1/16W) ±100ppm/C Pad SMD Automotive T/R | R3, R5 | DNP | 2

Microchip MIC5504-2.8YM5-TR | Single 300mA LDO withU 1 | | | 1

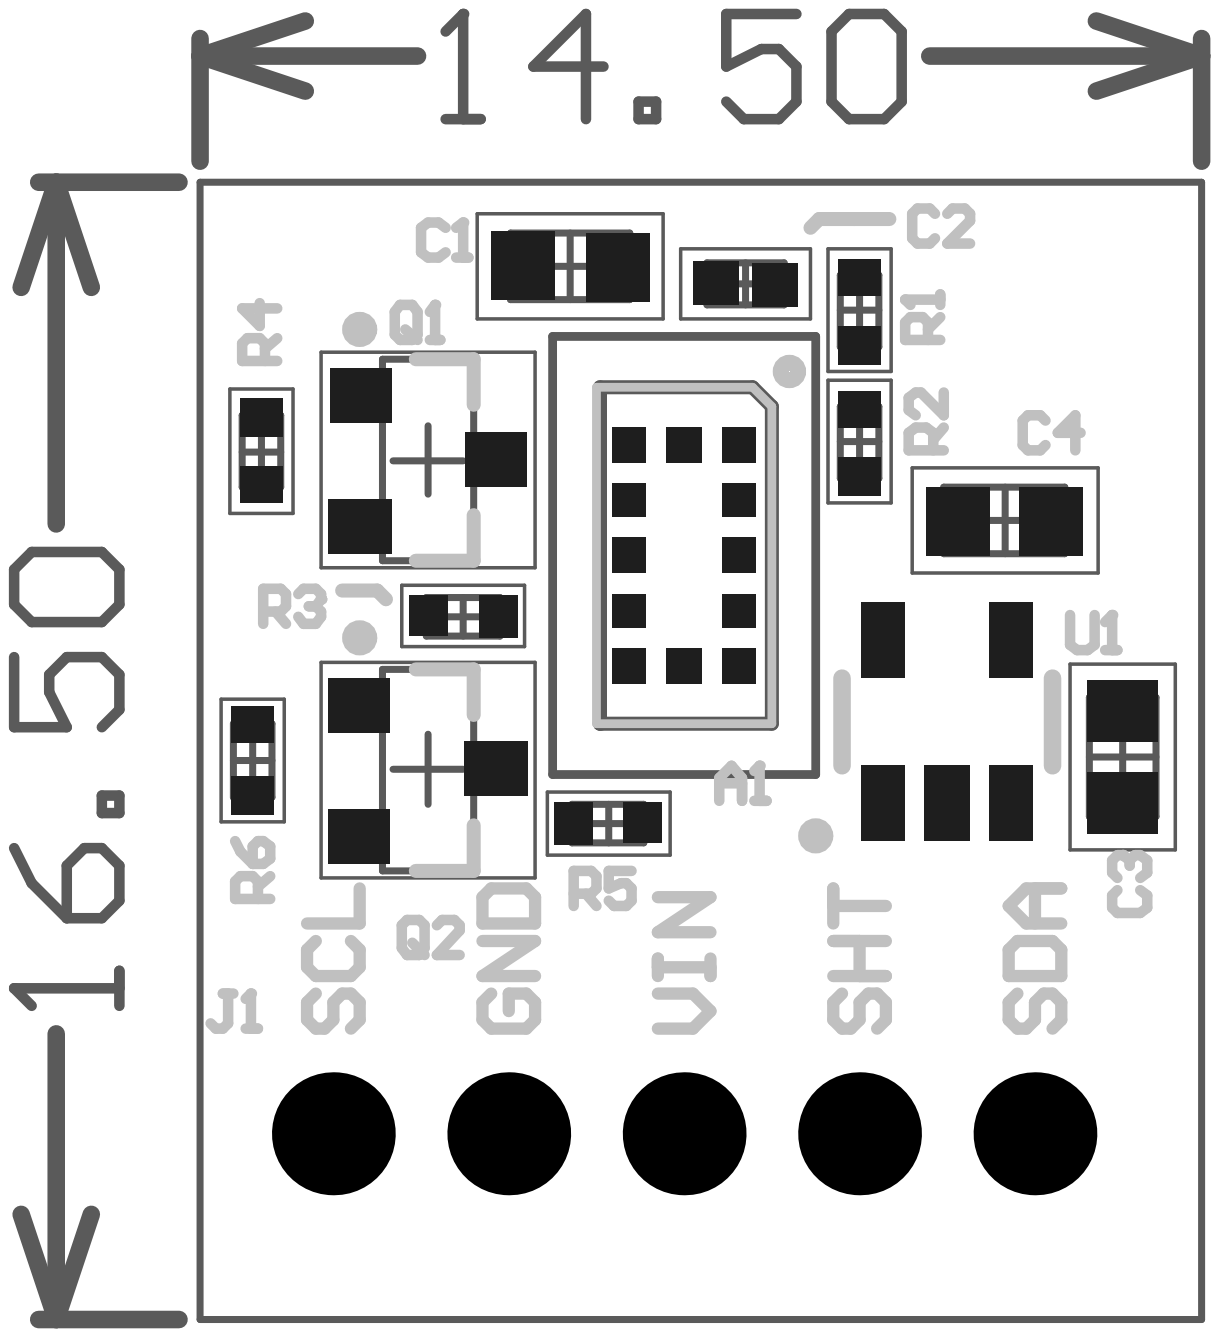
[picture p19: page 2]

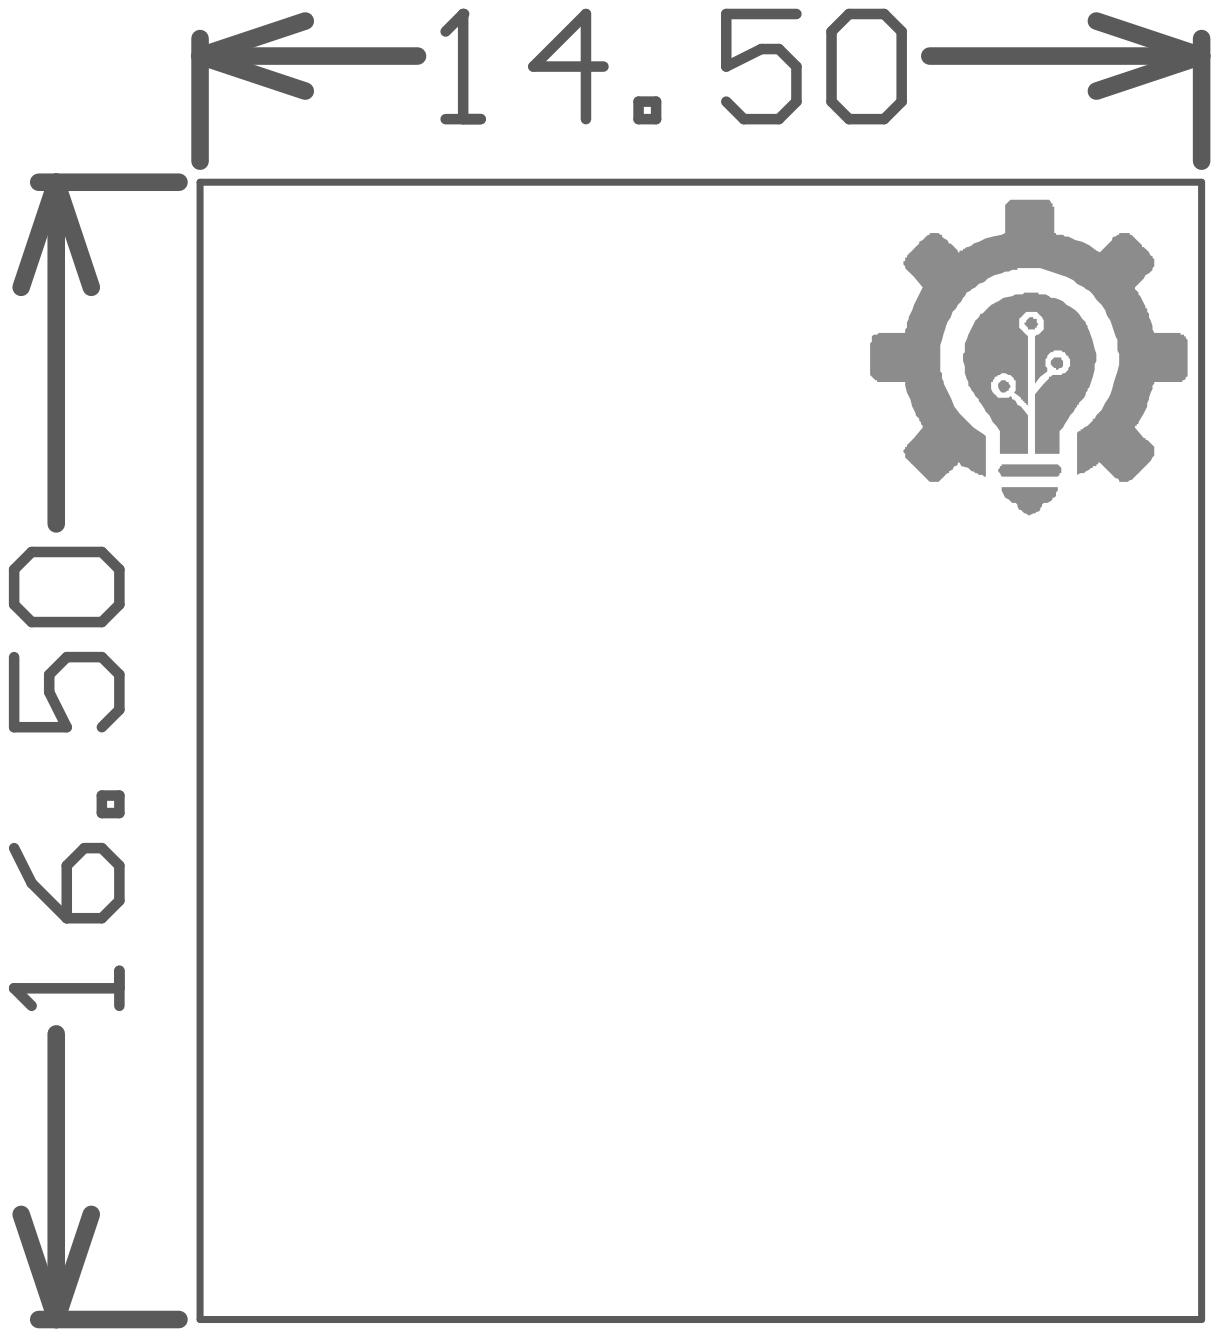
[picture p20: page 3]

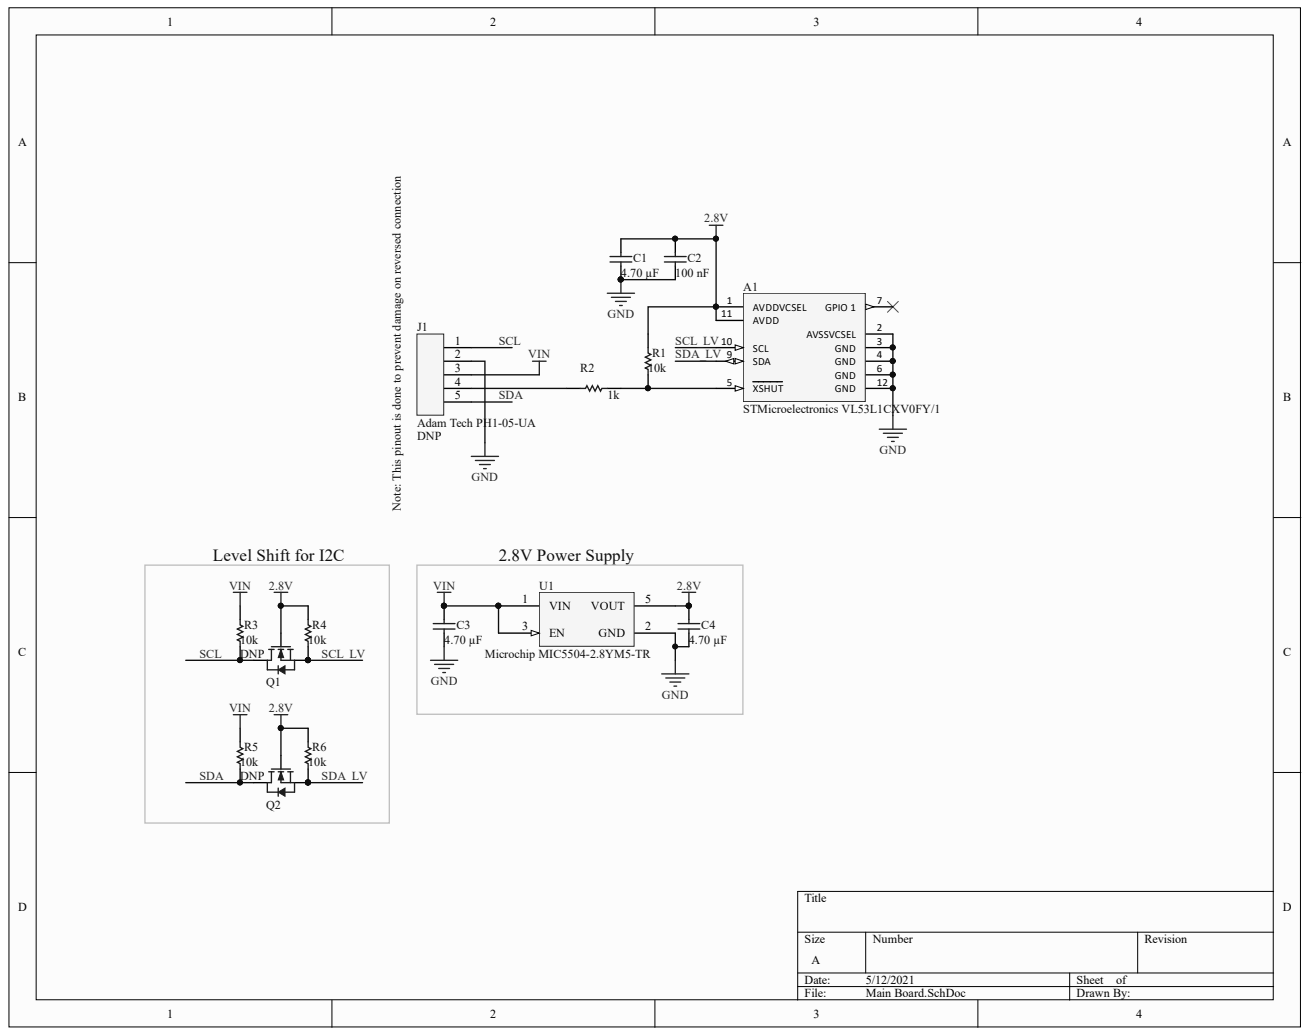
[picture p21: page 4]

Note: This pinout is done to prevent damage on reversed connection

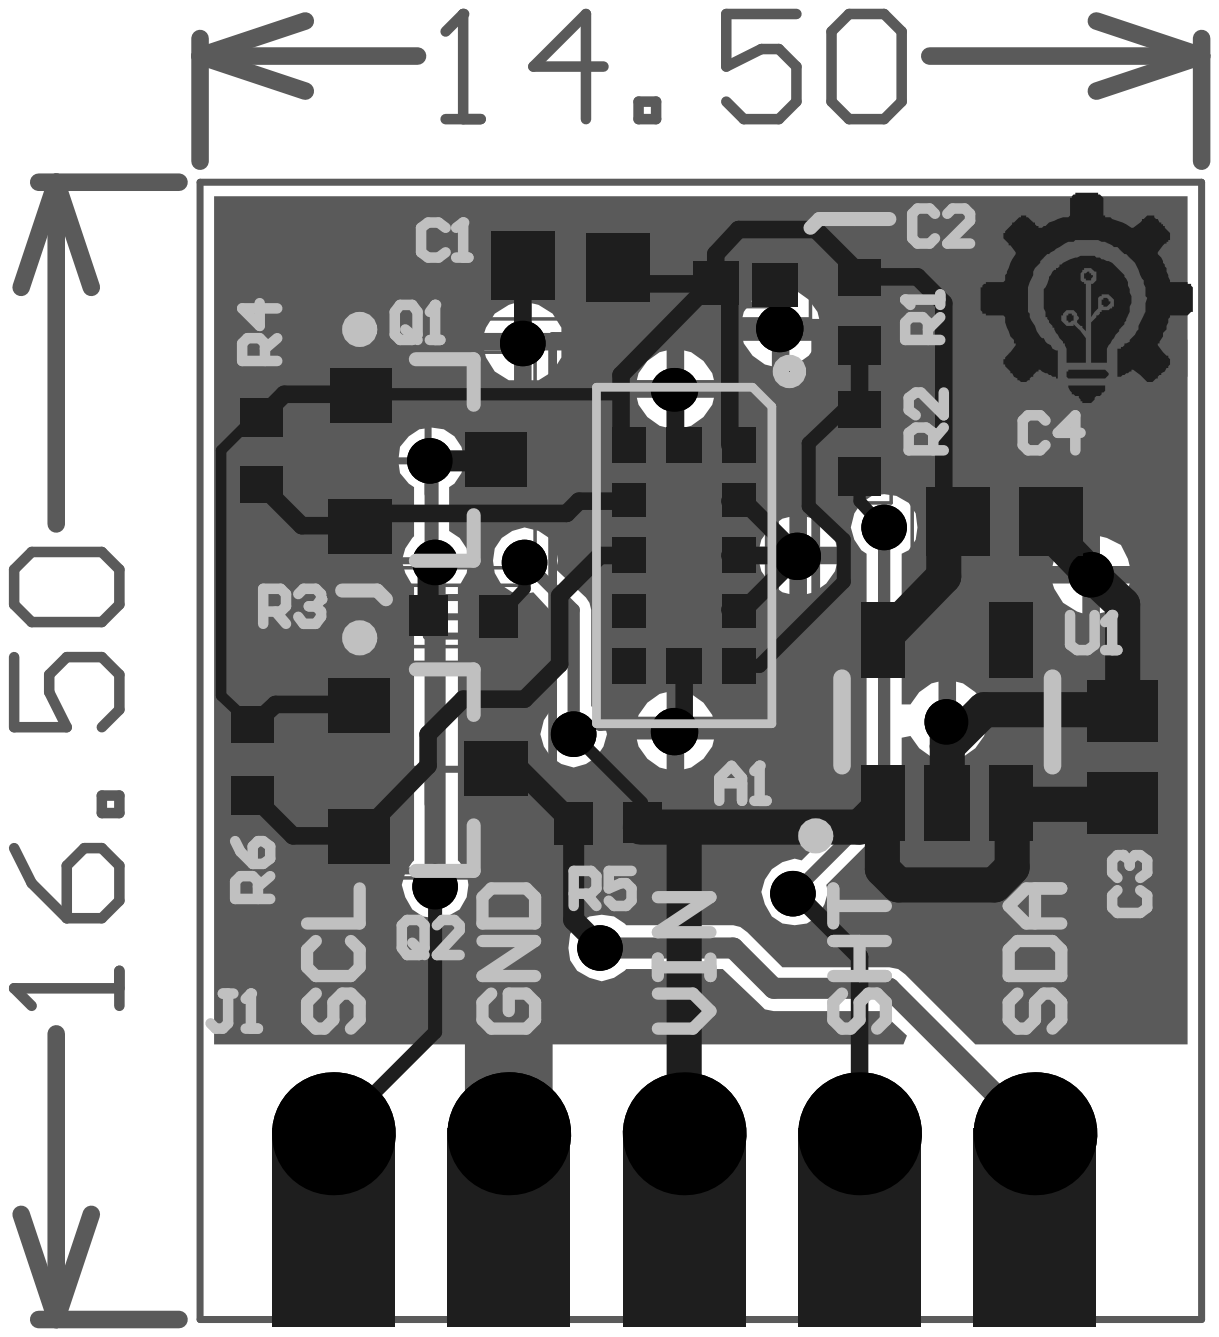
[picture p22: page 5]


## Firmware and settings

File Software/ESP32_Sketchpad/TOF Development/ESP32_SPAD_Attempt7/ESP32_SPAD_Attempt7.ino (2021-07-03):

/*
   Version History
   version: May 12, 2021 2:15am
   - these library functions work: https://github.com/pololu/vl53l1x-arduino, ST Library function fail here: https://github.com/pololu/vl53l1x-st-api-arduino/blob/master/vl53l1x-st-api/vl53l1x-st-api.ino
   - going to try setROISize, setROICenter from pololu arduino library with short distance mode, 50ms timing budget, 55ms inter period

 *  * version: May 12, 2021 2:15am
   - previous version works well to get single spad. this version will try to connect to ROS bridge
   -
*/


#include <Wire.h>

#include <VL53L1X.h>  // from pololu library

#include <WiFi.h>
#include <WebServer.h>
#include <WebSocketsClient.h>
#include <ArduinoJson.h>
#include <EEPROM.h>

#define EEPROM_SIZE 34

VL53L1X sensor;
/*
  This includes wifi credentials, ensuring they are not checked into a repo

  1. Create a file called "wifi.h" in the same folder
  2. Place the following text in the file:
  #define HOME_SSID "replace with your wifi ssid"
  #define PWD "replace your wifi password"
  #define IP "replace with your laptop's IP"
  3. Save.
*/
#include "wifi_details.h"

#define MEASUREMENT_BUDGET_MS 15000

int TOF_discovered_flag = 0; // set to 1 when the TOF address 0x29 is discovered
int initialize_once_flag = 0; // used so the TOF sensor is initialized once
int success_flag = 0;

uint8_t ROI_width;
uint8_t  ROI_height;
uint8_t  ROI_center;
float distance_in_meters = 0;
uint32_t distance_in_millimeters = 0;


WebSocketsClient webSocket; // this is a websocket client object
char buffer[800];
struct timeval tv; //handles setting and getting time

String tx_array_string = "";
String nextdata_string = "";

//uint8_t topright_spad_centers[16] = {27, 14, 42, 46, 74, 78, 106, 110, 145, 149, 177, 181, 209, 213, 241, 245};
uint8_t left2right_top2down_spad_centers[16] = {145, 177, 209, 241, 149, 181, 213, 245, 110, 78, 46, 14, 106, 74, 42, 10};


uint8_t spad_center_index = 0;

int16_t calibrated_offsets[16];

void setup()
{

  byte error, address;
  int nDevices;

  EEPROM.begin(EEPROM_SIZE);

  Wire.begin(25, 23); //Join I2C bus, set SDA and SCL pins respectively (tested on ESP32, remove pins if using another chip)
  Wire.setClock(400000); //Set speed to 400Khz, chip supports up to 1Mhz

  Serial.begin(115200);
  while (!Serial);             // Leonardo: wait for serial monitor
  Serial.println("\nI2C Scanner");

  Serial.println("Scanning...");

  nDevices = 0;
  for (address = 1; address < 127; address++ )
  {
    // The i2c_scanner uses the return value of
    // the Write.endTransmisstion to see if
    // a device did acknowledge to the address.
    Wire.beginTransmission(address);
    error = Wire.endTransmission();

    if (error == 0)
    {
      Serial.print("I2C device found at address 0x");
      if (address < 16)
        Serial.print("0");
      Serial.print(address, HEX);
      Serial.println("  !");

      if (address == 41)
      {
        Serial.println("VL53L1X discovered  !");
        TOF_discovered_flag = 1;
      }

      nDevices++;
    }
    else if (error == 4)
    {
      Serial.print("Unknown error at address 0x");
      if (address < 16)
        Serial.print("0");
      Serial.println(address, HEX);
    }
  }
  if (nDevices == 0)
    Serial.println("No I2C devices found\n");
  else
    Serial.println("done\n");

  delay(2000);           // wait 5 seconds for next scan

  // **********
  // after finding the address, initialize the sensor
  // **********

  if (TOF_discovered_flag == 1)
  {
    if (!sensor.init())
    {
      Serial.println("Failed to detect and initialize sensor!");
      success_flag = 0;
    }
    else
    {
      Serial.println("VL53L1X is initialized");

      sensor.setDistanceMode(VL53L1X::Medium);

      // ********
      // set ROIs
      // ********
      sensor.getROISize(&ROI_width, &ROI_height);
      Serial.printf("original width: %d, original height: %d \n", ROI_width, ROI_height);
      ROI_center = sensor.getROICenter();
      Serial.printf("original center: %d \n", ROI_center);

      // the ROi will be 4 x 4, around the center ROI number of 199
      //sensor.setROISize(4, 4);
      //sensor.setROICenter(207);

      // check for change
      sensor.getROISize(&ROI_width, &ROI_height);
      Serial.printf("new width: %d, new height: %d \n", ROI_width, ROI_height);
      ROI_center = sensor.getROICenter();
      Serial.printf("new center: %d \n", ROI_center);

      // ********
      // set timing budget and inter-measurement period
      // ********
      sensor.setMeasurementTimingBudget(MEASUREMENT_BUDGET_MS);
      sensor.startContinuous(MEASUREMENT_BUDGET_MS + 4000);  // intermeasurement period must be timing budget + 4ms at minimum
      success_flag = 1;  // allow for continuous reading

    }


  }

  // **********
  // wifi connection
  // **********

  WiFi.begin(HOME_SSID, PWD);

  while (WiFi.status() != WL_CONNECTED) // if it's not connected to home wi-fi
  {
    Serial.print(".");
    delay(500);
  }

  Serial.println("");
  Serial.print("IP Address: ");
  Serial.println(WiFi.localIP());

  webSocket.begin(IP, 9090, "/");  // on server side, run the begin method within the websocket object
  webSocket.onEvent(webSocketEvent); // if a request happens to the server, trigger this function
  webSocket.setReconnectInterval(1000);

  //calibrate_allspads() // only uncomment if ready to calibrate TOF sensor against flat surface
  retrieve_EEPROM_data(calibrated_offsets);   // EEPROM values should be zero if the ESP32 has never has the EEPROM written to 

}


void loop()
{




  webSocket.loop();


  if (spad_center_index == 16)
  {
    spad_center_index = 0;
  }

  if (success_flag == 1)
  {


    sensor.readSingle(false);  // start single measurement

    while (!sensor.dataReady()) {
      //wait for sensor data
    }

    sensor.setROISize(4, 4);
    sensor.setROICenter(left2right_top2down_spad_centers[spad_center_index]);


    //distance_in_mm = sensor.read(false) / 1000.0;
    //distance_in_millimeters = (uint32_t)(sensor.read(false));
    distance_in_millimeters = (uint32_t)(((int16_t)sensor.read(false)) + calibrated_offsets[spad_center_index]);

    distance_in_meters = distance_in_millimeters/1000.0;
    //Serial.printf("spad_index: %d, spad center: %d, distance is: %f \n", spad_center_index, topright_spad_centers[spad_center_index], distance_in_mm );

    nextdata_string = String(distance_in_meters);
    tx_array_string += String(distance_in_meters);

    if (spad_center_index != 15)
    {
      tx_array_string += String(",");
    }


    if (sensor.timeoutOccurred())
    {
      Serial.printf(" TIMEOUT \n");
    }



    if (spad_center_index >= 15)
    {
      spad_center_index = 0;

      Serial.printf("transmitting following data string \n");
      Serial.println(tx_array_string);

      //json_Pub_TOF_A["msg"]["data"] = "0";
      //json_Pub_TOF_A["msg"]["data"] = tx_array_string;
      //serializeJsonPretty(json_Pub_TOF_A, Serial);
      //String val = "1000,2000,3000,4000,5000,6000,7000,8000,9000,1000,11000,12000,13000,14000,15000,16000";
      //json_Pub_TOF_A["msg"]["data"]= val;
      StaticJsonDocument<800> json_Pub_TOF_A;
      json_Pub_TOF_A["op"] = "publish";
      json_Pub_TOF_A["id"] = "2";
      json_Pub_TOF_A["topic"] = "/Shelly/TOF_A";
      json_Pub_TOF_A["type"] = "std_msgs/String";
      json_Pub_TOF_A["msg"]["data"] = tx_array_string;
      webSocket.sendTXT(buffer, serializeJson(json_Pub_TOF_A, buffer));
      //json_Pub_TOF_A["msg"]["data"]="1,2,3,4,5,6,7,8,9,10,11,12,13,14,15,16";

      tx_array_string = "";
      nextdata_string = "";
    }
    else
    {
      spad_center_index++;

    }



  }
  else
  {
    Serial.println("Failure :(");
    delay(2000);
  }

}



void webSocketEvent(WStype_t type, uint8_t * payload, size_t length) {
  char *payload_pointer = (char *)payload;

  //Serial.printf("Got Type %i\n", type);

  switch (type) {
    case WStype_ERROR: // type 0
      {
        Serial.println("Websocket Error");
        break;
      }
    case WStype_DISCONNECTED: // type
      {
        Serial.printf("[WSc] Disconnected from url: %s\n", IP);
        break;
      }
    case WStype_CONNECTED: // type 2
      {
        Serial.printf("[WSc] Connected to url: %s\n", IP);

        //SUBSCRIBERS
        // Receives Header from ROS on laptop, used to set time and check connection
        StaticJsonDocument<800> json_Sub_header;
        json_Sub_header["op"] = "subscribe";
        json_Sub_header["id"] = "1";
        json_Sub_header["topic"] = "/Shelly/header_sent";
        json_Sub_header["type"] = "std_msgs/Header";

        //PUBLISHERS
        //Publishes TOF data from Shelly to Laptop
        StaticJsonDocument<800> json_Pub_TOF_A;
        json_Pub_TOF_A["op"] = "advertise";
        json_Pub_TOF_A["id"] = "2";
        json_Pub_TOF_A["topic"] = "/Shelly/TOF_A";
        json_Pub_TOF_A["type"] = "std_msgs/String";

        //Subscribe to stuff
        webSocket.sendTXT(buffer, serializeJson(json_Sub_header, buffer));
        //Advertise Publishers
        webSocket.sendTXT(buffer, serializeJson(json_Pub_TOF_A, buffer));

        break;
      }
    case WStype_TEXT: // type 3
      {
        StaticJsonDocument<800> json_recievedmessage;
        DeserializationError err = deserializeJson(json_recievedmessage, payload_pointer);

        if (err)
        {
          Serial.print("Error: deserializeJson() returned: ");
          Serial.println(err.c_str());
        }
        else
        {
          String topic  = json_recievedmessage["topic"];
          if (topic == "/Shelly/header_sent")
          {
            //serializeJsonPretty(json_recievedmessage, Serial);
            //int seq  = json_recievedmessage["msg"]["seq"];
            //Serial.println(seq);
            gettimeofday(&tv, NULL);
            //            Serial.print ("-----> Was ");
            //            Serial.print (tv.tv_sec);
            //            Serial.print (" ");
            //            Serial.print (tv.tv_usec);
            struct timeval tv_new;
            tv_new.tv_sec = json_recievedmessage["msg"]["stamp"]["secs"];
            tv_new.tv_usec = (int)json_recievedmessage["msg"]["stamp"]["nsecs"] / 1000;
            settimeofday(&tv_new, NULL);
            //            Serial.print ("    Is ");
            //            Serial.print (tv.tv_sec);
            //            Serial.print (" ");
            //            Serial.print (tv.tv_usec);
            //            Serial.println("");
          }
        }
      }
    default:
      break;
  }

}



void retrieve_EEPROM_data(int16_t *data_array_pointer)
{
    uint8_t  read_lowbyte   = 0;
    uint8_t  read_highbyte  = 0;
    uint16_t read_spad_data = 0;

    int negative_true_flag = 0;

    int data_count = 0;
    int count = 0;
    
    while(count < 32)
    {
      if((count % 2 == 0))
      {
        data_count = count/2;
        read_highbyte = (uint8_t)EEPROM.read(count);

 
        if(read_highbyte >= 0x80)
        {
          //Serial.printf("negative read_highbyte: %d || ",read_highbyte);
          negative_true_flag = 1;
          read_highbyte = read_highbyte & ~(0x80);  // remove the 1 set to indicate a negative
          //Serial.printf("new read_highbyte: %d \n ",read_highbyte);         
        }
        else
        {
          negative_true_flag = 0;
        }
        
        count++;
        read_lowbyte  = (uint8_t)EEPROM.read(count); 
        count++;   

        //Serial.printf("lowbyte: %d \n ",read_lowbyte); 
        
        read_spad_data = (uint16_t)(read_highbyte << 8);
        read_spad_data = (uint16_t)(read_spad_data + read_lowbyte);


        //Serial.printf("read_spad_data: %d \n ",read_spad_data); 
 
        if(negative_true_flag == 1)
        {
          //Serial.printf("[%d]read_spad_data: - %d || ",data_count,read_spad_data); 
          data_array_pointer[data_count] = (int16_t)(-1*(int16_t)(read_spad_data));
          //Serial.printf("data_array_pointer[%d] = %d \n",data_count,data_array_pointer[data_count]); 
        }
        else
        {
          //Serial.printf("[%d]read_spad_data: + %d || ",data_count,read_spad_data);
          data_array_pointer[data_count] = (int16_t)(read_spad_data);
          //Serial.printf("data_array_pointer[%d] = %d \n",data_count,data_array_pointer[data_count]); 
          
        }

        Serial.printf("EEPROM readback data[%d]: %d \n",data_count,data_array_pointer[data_count]);        
      }   
    }  

  



}


float to_degrees(float rad)
{
  return rad * (180.0 / M_PI);
  
}

float to_rad(float degrees)
{
  return (degrees * M_PI)/180.0;
  
}

void calibrate_allspads()
{

   float spad_avg[32]; 
   float spad_current_data[16];   
   float spad_avg_old[32] = {0,0,0,0,0,0,0,0,0,0,0,0,0,0,0,0,0,0,0,0,0,0,0,0,0,0,0,0,0,0,0,0};
   int num_of_elements = 1;
   float calibrated_differences[16] = {0,0,0,0,0,0,0,0,0,0,0,0,0,0,0,0}; // the error for each SPAD location

   uint8_t low_byte = 0;
   uint8_t high_byte = 0;
   uint16_t spad_diff = 0; 
   int16_t negative_value_check = 0;


  int theta = 0;                  // horizontal angle in degrees, positive right
  int phi = 0;                    // vertical angle in degrees, positive down

  // *********************
  // During Calibration, this is the distance between the TOF sensor and flat wall 
  float flat_distance = 140.0;     // in mm - 14cm = 140mm
  // ********************* 

  float L2R_T2B_distances[32];
  float z = flat_distance;        // axis straight ahead
  float a = 0;                    //distance vector projected on the X-Z plane
  float sub_angle = 27.0/8.0;     
  
  int count = 0;
  int data_count = 0;

  // *********************
  // find the theoretical hypotenuse distances away from flat surface for each of the 16 SPADs
  // *********************
    
  Serial.printf("Calculating true distances given %f mm away flat surface \n",flat_distance);

  for (theta = -3; theta < 4; theta = theta + 2)
  {
    a = z/cos(to_rad(theta*sub_angle)); 
    
    for(phi = -3; phi < 4; phi = phi+ 2)
    {
      L2R_T2B_distances[count] = a/cos(to_rad(phi*sub_angle));
      
      Serial.printf("t:%d, p: %d, L2R_T2B_distances[%d] = %f \n",theta,phi,count,L2R_T2B_distances[count]);
      count++;  // should only go up to 15
    }
    
  }


  // *********************
  // find the average sensor reading for each of the 16 SPADs  over 50 readings
  // *********************
  
    Serial.printf("Taking 50 samples of each 16 ROIs to find average reported distance... \n");

    sensor.readSingle(false);  // start single measurement

    while (!sensor.dataReady()) {
      //wait for sensor data
    }

    sensor.setROISize(4, 4);


   for(int i1 = 0; i1 < 50; i1++)  // take 50 samples of each SPAD to find the average reading of each SPAD
   {
      Serial.printf("sample: %d \n",i1);  
      for(int i2 = 0; i2 < 16; i2++ )  // for each of the 16 SPADS SPAD
      {

         sensor.setROISize(4, 4);
         sensor.setROICenter(left2right_top2down_spad_centers[i2]);  // uint8_t left2right_top2down_spad_centers[16] = {145, 177, 209, 241, 149, 181, 213, 245, 110, 78, 46, 14, 106, 74, 42, 10};
                 
         // get the reading for that SPAD
          sensor.readSingle(false);  // start single measurement
      
          while (!sensor.dataReady()) {
            //wait for sensor data
          }

         spad_current_data[i2] = (float)(sensor.read(false));  // sensor.read(false) returns in units of millimeters (14cm = "140")

         // New average = old average * (n-1)/n + new value /n
         spad_avg[i2] = spad_avg_old[i2]*((float)num_of_elements - 1)/(float)num_of_elements + spad_current_data[i2]/(float)num_of_elements;

         spad_avg_old[i2] =  spad_avg[i2];   
      }

        
        
      num_of_elements++;  
    
   }


  // *********************
  // find the difference between average SPAD reading and the calculated theoritical distance
  // then save the 16 different 16-bit values in 32 8-bit EEPROM memory addresses
  // *********************

    Serial.printf("find offsets between average and true distances and save in EEPROM... \n");
    count = 0;
    while(count < 32)
    {
      
      if((count % 2 == 0) && (count >= 0))
      {
         data_count = count/2;
          // error_diff = real - measured (to get back real = measured + error_diff_fromEEPROM)
         negative_value_check = (int16_t)(L2R_T2B_distances[data_count] - spad_avg[data_count]);

         if(negative_value_check < 0)
         {

            calibrated_differences[data_count] = negative_value_check;

            spad_diff = (uint16_t)(-1*negative_value_check) ; 
            high_byte = (uint8_t)(spad_diff  >> 8);
            high_byte =  high_byte | (0x80);              // set MSB to 1 if value is negative


            Serial.printf("spad_avg: %f, real: %f, calibrated_differences[%d]: %f \n",spad_avg[data_count],L2R_T2B_distances[data_count],data_count,calibrated_differences[data_count]);

         }
         else
         {

            calibrated_differences[data_count] = negative_value_check;  // ?? set MSB if negative
           
            spad_diff = (uint16_t)negative_value_check ; 
            high_byte = (uint8_t)(spad_diff  >> 8);

            Serial.printf("spad_avg: %f, real: %f, calibrated_differences[%d]: %f \n",spad_avg[data_count],L2R_T2B_distances[data_count],data_count,calibrated_differences[data_count]);
           
         }

         low_byte  = (uint8_t)(spad_diff & 0x00FF);

        EEPROM.write(count,high_byte);
        count++;
        EEPROM.write(count,low_byte);  
        count++;     
                
      } 

      
    }

    EEPROM.commit(); 




}

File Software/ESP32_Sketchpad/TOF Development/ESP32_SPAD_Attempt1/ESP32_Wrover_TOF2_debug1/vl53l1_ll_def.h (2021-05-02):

/*
* Copyright (c) 2017, STMicroelectronics - All Rights Reserved
*
* This file is part of VL53L1 Core and is dual licensed,
* either 'STMicroelectronics
* Proprietary license'
* or 'BSD 3-clause "New" or "Revised" License' , at your option.
*
********************************************************************************
*
* 'STMicroelectronics Proprietary license'
*
********************************************************************************
*
* License terms: STMicroelectronics Proprietary in accordance with licensing
* terms at www.st.com/sla0081
*
* STMicroelectronics confidential
* Reproduction and Communication of this document is strictly prohibited unless
* specifically authorized in writing by STMicroelectronics.
*
*
********************************************************************************
*
* Alternatively, VL53L1 Core may be distributed under the terms of
* 'BSD 3-clause "New" or "Revised" License', in which case the following
* provisions apply instead of the ones mentioned above :
*
********************************************************************************
*
* License terms: BSD 3-clause "New" or "Revised" License.
*
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
* 3. Neither the name of the copyright holder nor the names of its contributors
* may be used to endorse or promote products derived from this software
* without specific prior written permission.
*
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
*
********************************************************************************
*
*/

/**
 * @file vl53l1_ll_def.h
 *
 * @brief Type definitions for VL53L1 LL Driver.
 *
 */


#ifndef _VL53L1_LL_DEF_H_
#define _VL53L1_LL_DEF_H_

#include "vl53l1_ll_device.h"
#include "vl53l1_error_codes.h"
#include "vl53l1_register_structs.h"
#include "vl53l1_platform_user_config.h"
#include "vl53l1_platform_user_defines.h"
#include "vl53l1_error_exceptions.h"

#ifdef __cplusplus
extern "C" {
#endif

/** @defgroup VL53L1_globalLLDriverDefine_group VL53L1 Defines
 *  @brief    VL53L1 LL Driver Defines
 *  @{
 */

/** VL53L1 Low Level Driver IMPLEMENTATION major version */
#define VL53L1_LL_API_IMPLEMENTATION_VER_MAJOR       1
/** VL53L1 Low Level DriverI IMPLEMENTATION minor version */
#define VL53L1_LL_API_IMPLEMENTATION_VER_MINOR       2
/** VL53L1 Low Level DriverI IMPLEMENTATION sub version */
#define VL53L1_LL_API_IMPLEMENTATION_VER_SUB         10
/** VL53L1 Low Level Driver IMPLEMENTATION sub version */
#define VL53L1_LL_API_IMPLEMENTATION_VER_REVISION    1840

#define VL53L1_LL_API_IMPLEMENTATION_VER_STRING "1.2.11.1840"

/** VL53L1_FIRMWARE min and max compatible revisions */
#define VL53L1_FIRMWARE_VER_MINIMUM         398
#define VL53L1_FIRMWARE_VER_MAXIMUM         400


/****************************************
 * PRIVATE define do not edit
 ****************************************/

#define VL53L1_LL_CALIBRATION_DATA_STRUCT_VERSION       0xECAB0102
    /** VL53L1 Calibration Data struct version */

/* Start Patch_ZoneCalDataStructVersion_11854 */

#define VL53L1_LL_ZONE_CALIBRATION_DATA_STRUCT_VERSION  0xECAE0101
    /** VL53L1 Zone Calibration Data struct version */

/* End Patch_ZoneCalDataStructVersion_11854 */

#define VL53L1_MAX_OFFSET_RANGE_RESULTS       3
	/*!< Sets the maximum number of offset range results
		 required for the offset calibration.
		 Order is RANGE, MM1, MM2  */

#define VL53L1_NVM_MAX_FMT_RANGE_DATA         4
	/*!< The number of FMT range data points stored in NVM */

#define VL53L1_NVM_PEAK_RATE_MAP_SAMPLES  25
    /*!< The number of samples in the NVM peak rate signal map */
#define VL53L1_NVM_PEAK_RATE_MAP_WIDTH     5
    /*!< Array width of NVM peak rate signal map */
#define VL53L1_NVM_PEAK_RATE_MAP_HEIGHT     5
    /*!< Array height the NVM peak rate signal map */

/** @defgroup VL53L1_defineExtraError_group Error and Warning code returned by API
 *  The following DEFINE are used to identify the PAL ERROR
 *  @{
 */

#define VL53L1_ERROR_DEVICE_FIRMWARE_TOO_OLD           ((VL53L1_Error) - 80)
	/*!< Device Firmware too old .. */
#define VL53L1_ERROR_DEVICE_FIRMWARE_TOO_NEW           ((VL53L1_Error) - 85)
	/*!< Device Firmware too new .. */
#define VL53L1_ERROR_UNIT_TEST_FAIL                    ((VL53L1_Error) - 90)
	/*!< Unit Test Fail */
#define VL53L1_ERROR_FILE_READ_FAIL                    ((VL53L1_Error) - 95)
	/*!< File Read  Fail */
#define VL53L1_ERROR_FILE_WRITE_FAIL                   ((VL53L1_Error) - 96)
	/*!< File Write Fail */
	/*!< Tells requested functionality has not been implemented yet or
	 * not compatible with the device */
/** @} VL53L1_defineExtraError_group */


/** @brief Defines the parameters of the LL driver Get Version Functions
 */
typedef struct {
	uint32_t     ll_revision; /*!< revision number */
	uint8_t      ll_major;    /*!< major number */
	uint8_t      ll_minor;    /*!< minor number */
	uint8_t      ll_build;    /*!< build number */
} VL53L1_ll_version_t;


/** @brief Reference SPAD Characterization (RefSpadChar) Config
 */
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

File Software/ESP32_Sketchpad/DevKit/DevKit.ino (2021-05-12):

/*
  Devkit testing software for Shelly
  By: Ilia Baranov
  BLueprint Foundry
  Date: April 30th, 2021
  License: BSD 3 Clause
*/

#include <Wire.h>
#include <PI4IOE5V96248.h>
#include <EAAPMST3923A2.h>
#include <Arduino-MAX17055_Driver.h>
#include <ICM_20948.h>
#include <WiFi.h>
#include <WebServer.h>
#include <WebSocketsClient.h>
#include <ArduinoJson.h>
#include <time.h> //TODO: Time is not being kept without a constant header stream... Hmm...

WebSocketsClient webSocket; // this is a websocket client object

/*
  This includes wifi credentials, ensuring they are not checked into a repo

  1. Create a file called "wifi.h" in the same folder
  2. Place the following text in the file:
  #define HOME_SSID "replace with your wifi ssid"
  #define PWD "replace your wifi password"
  #define IP "replace with your laptop's IP"
  3. Save.
*/
#include "wifi_details.h"

// Subscribers and Publishers over Webscokets/Rosbridge/JSON
//Specifications: https://github.com/RobotWebTools/rosbridge_suite/blob/develop/ROSBRIDGE_PROTOCOL.md
char buffer[400];
StaticJsonDocument<400> json_Subscribe_header_sent;
StaticJsonDocument<400> json_Sub_cmd_vel;
StaticJsonDocument<400> json_recievedmessage;
StaticJsonDocument<400> json_Publish_IMU;
StaticJsonDocument<400> json_Publish_IMU_Temp;

void TaskMotors( void *pvParameters );
void TaskBlank( void *pvParameters );

struct timeval tv; //handles setting and getting time

PI4IOE5V96248 io_exp; // Object for communicating with the io expander
const byte PI4IOE5V96248_ADDRESS = 0x23;  // Example PI4IOE5V96248 I2C address, depends on setting for AD0, AD1, AD2
ICM_20948_I2C IMU;
MAX17055 battery;

// the setup function runs once when you press reset or power the board
void setup() {

  SetupJSON();

  // initialize serial communication at 115200 bits per second:
  Serial.begin(115200);

  Serial.print("Attempting to connect:");

  WiFi.begin(HOME_SSID, PWD);

  while (WiFi.status() != WL_CONNECTED) // if it's not connected to home wi-fi
  {
    Serial.print(".");
    delay(500);
  }

  Serial.println("");
  Serial.print("IP Address: ");
  Serial.println(WiFi.localIP());

  Wire.begin(25, 23); //Join I2C bus, set SDA and SCL pins respectively
  Wire.setClock(400000); //Set speed to 400Khz

  delay(50); //give system chance to stabilize, likely not needed.

  SetupSensors();

  webSocket.begin(IP, 9090, "/");  // on server side, run the begin method within the websocket object
  webSocket.onEvent(webSocketEvent); // if a request happens to the server, trigger this function
  webSocket.setReconnectInterval(1000);

  // Now set up two tasks to run independently.
  xTaskCreatePinnedToCore(
    TaskMotors
    ,  "TaskBlink"   // A name just for humans
    ,  1024  // This stack size can be checked & adjusted by reading the Stack Highwater
    ,  NULL
    ,  2  // Priority, with 3 (configMAX_PRIORITIES - 1) being the highest, and 0 being the lowest.
    ,  NULL
    ,  1); //Motors has to be on core 1 to work...?

  xTaskCreatePinnedToCore(
    TaskBlank
    ,  "TaskBlank"
    ,  2048  // Stack size
    ,  NULL
    ,  1  // Priority
    ,  NULL
    ,  1);

  // Now the task scheduler, which takes over control of scheduling individual tasks, is automatically started.
}

void loop()
{
  webSocket.loop();
}

/*--------------------------------------------------*/
/*---------------------- Tasks ---------------------*/
/*--------------------------------------------------*/
void webSocketEvent(WStype_t type, uint8_t * payload, size_t length) {
  char *payload_pointer = (char *)payload;

  //Serial.printf("Got Type %i\n", type);

  switch (type) {
    case WStype_ERROR: // type 0
      {
        Serial.println("Websocket Error");
        break;
      }
    case WStype_DISCONNECTED: // type
      {
        Serial.printf("[WSc] Disconnected from url: %s\n", IP);
        break;
      }
    case WStype_CONNECTED: // type 2
      {
        Serial.printf("[WSc] Connected to url: %s\n", IP);
        //Subscribe to stuff
        webSocket.sendTXT(buffer, serializeJson(json_Subscribe_header_sent, buffer));
        webSocket.sendTXT(buffer, serializeJson(json_Sub_cmd_vel, buffer));
        //Advertise Publishers
        //len = serializeJson(json_Publish_IMU, buffer);
        webSocket.sendTXT(buffer, serializeJson(json_Publish_IMU, buffer));
        json_Publish_IMU["op"] = "publish";
        webSocket.sendTXT(buffer, serializeJson(json_Publish_IMU_Temp, buffer));
        json_Publish_IMU_Temp["op"] = "publish";

        break;
      }
    case WStype_TEXT: // type 3
      {
        webSocket.sendTXT(buffer, serializeJson(json_Publish_IMU, buffer)); //TODO: How to send outside of Websocket event??
        webSocket.sendTXT(buffer, serializeJson(json_Publish_IMU_Temp, buffer));

        DeserializationError err = deserializeJson(json_recievedmessage, payload_pointer);

        if (err)
        {
          Serial.print("Error: deserializeJson() returned: ");
          Serial.println(err.c_str());
        }
        else
        {
          String topic  = json_recievedmessage["topic"];
          if (topic == "/Shelly/header_sent")
          {
            //serializeJsonPretty(json_recievedmessage, Serial);
            //int seq  = json_recievedmessage["msg"]["seq"];
            //Serial.println(seq);
            gettimeofday(&tv, NULL);
            //            Serial.print ("-----> Was ");
            //            Serial.print (tv.tv_sec);
            //            Serial.print (" ");
            //            Serial.print (tv.tv_usec);
            struct timeval tv_new;
            tv_new.tv_sec = json_recievedmessage["msg"]["stamp"]["secs"];
            tv_new.tv_usec = (int)json_recievedmessage["msg"]["stamp"]["nsecs"] / 1000;
            settimeofday(&tv_new, NULL);
            //            Serial.print ("    Is ");
            //            Serial.print (tv.tv_sec);
            //            Serial.print (" ");
            //            Serial.print (tv.tv_usec);
            //            Serial.println("");
          }
          if (topic == "/Shelly/cmd_vel")
          {
            Serial.print(tv.tv_sec);
            Serial.print(" ");
            Serial.print("Shelly Moving: ");
            float cmd_x = json_recievedmessage["msg"]["linear"]["x"];
            float cmd_z = json_recievedmessage["msg"]["angular"]["z"];
            Serial.println(cmd_x);
          }
        }
      }
    default:
      break;
  }

}
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

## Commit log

2020-11-26 Adding first batch of production files
    [Shelly Main Board.GBL, Shelly Main Board.GBO, Shelly Main Board.GBP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]
2021-03-05 Adding Hardware info docs
    Also removed ESP8266 because we have switched to ESP32
2021-03-11 Just got wheels spinning
    Not sure why we have to use core 1 for motor control....
2021-03-12 Code tp Perform Speed Test
    this code contains the ESP8266 arduino code and the ROSBridge python node to perform a round trip up latency test with variable byte size
2021-03-12 TOF Sketch Added
    Added reference manuals and simple code to get data from the Sparkfun VL53L1X sensor with the ESP8266
    [VL53L1X_ULD_API_Example Run.cfg]
2021-03-24 Able to use vl54l1_api.c functions
    The SPAD attempt .ino is able to call functions in the ST VL53L1 Core API modified by Pololu Corporation to work on Arduino instead of an ST microcontroller. Able to use functions such as "VL53L1_Set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
2021-03-28 Bare Bones Spad v1.0.x
    Checking if this SPAD_Attempt.ino can retrieve one SPAD of data. If not, will have to remove "sensor.startContinuous(50)" library functions and replace with Polulu driver functions
    [SPAD_Attempt.ino]
2021-03-28 Using only polulu/ST library functions in SPAD Attempt 2 folder
    using only this code: https://github.com/pololu/vl53l1x-st-api-arduino, since we need the "VL53L1_SetUserROI" function. Read Shelly\Software\ESP32 Sketchpad\TOF Development\Reference\dm00474730-vl53l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
2021-04-02 Working Polulu 0x52 Example
    To prevent crashing firmware, close the serial monitor window before programming. In folder SPAD_Attempt3, I added a 5 second delay after the ESP8266 wakes up. this should give enough breathing room for the i2c sensor to wake up and be ready for i2c communication. I delayed the printing to the serial port to every 5 seconds since I suspect the arduino programming through serial port gets corrupted if it's also printing to the serial port. I suspect closing serial port monitor prevents TX RS232 on the ESP chip
    [vl53l1_api.c, vl53l1_api_strings.h, vl53l1_error_strings.h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]
2021-04-03 Spad calibration data v1.0.1
    able to get default user ROI and distance measurements using driver polling mode
2021-04-03 I THINK SPAD READING WORKSS!!!
    See code for ESP8266 in ESP32 Sketchpad\TOF Development\SPAD_Attempt3
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2021-04-14 Install esp32:esp32 platform correctly in CI workflow
2021-04-17 ESP32 Wrover communication works
    code in \Shelly\Software\ESP32 Sketchpad\TOF Development\ESP32_SPAD_Attempt1\ESp32Wrover_GetChipID_works\ESp32Wrover_GetChipID_works.ino
    works on ESP32 Wrover
2021-04-17 ESP32 Wrover fails at polling driver initiation
    the code \Shelly\Software\ESP32 Sketchpad\TOF Development\ESP32_SPAD_Attempt1\ESP32_Wrover_TOF1\ESP32_Wrover_TOF1.ino, states "VL53L1_StartMeasurement failed" after line 127, after the " // optional polling driver initiation" code. Time to find out which function is failing and why
    [ESP32_Wrover_TOF1.ino, vl53l1_api.c, vl53l1_api_strings.h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]
2021-04-17 ESP32 Wrover fails at I2C communication for get measurement update
    \Shelly\GitHub_Stuff\Shelly\Software\ESP32 Sketchpad\TOF Development\ESP32_SPAD_Attempt1\ESP32_Wrover_TOF2
    fails at line 160 status_int = VL53L1_GetRangingMeasurementData(Dev, &RangingData); //4mS
    but is able to get device information via I2C, with output:
    VL53L1X Model_ID: EA
    VL53L1X Module_Type: CC
    VL53L1X: EACC
    [ESP32_Wrover_TOF2.ino, vl53l1_api.c, vl53l1_api_strings.h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]
2021-04-25 I2C address check for failing ESP32 Wrover
    In C:\Users\ST\Documents\Electronics\Projects\Shelly\GitHub_Stuff\Shelly\Software\ESP32 Sketchpad\TOF Development\ESP32_SPAD_Attempt1\ESP32_Wrover_TOF2_debug1
    I added the lines:
    #include <VL53L1X.h>
    VL53L1X sensor;
    char device_i2c_address = 0;
    device_i2c_address = sensor.getAddress();
    Serial.printf("VL53L1X I2C address: %d \n",device_i2c_address);
    and got:
    VL53L1X I2C address: 41
    0x41 is not "Dev->I2cDevAddr = 0x52" or 0x29. Next step, use 0x41
    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
    [ESP32_Wrover_TOF2_debug1.ino, vl53l1_api.c, vl53l1_api_strings.h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]
2021-04-25 0x52 is only address that works with #include "vl53l1_api.h" example
    in: C:\Users\ST\Documents\Electronics\Projects\Shelly\GitHub_Stuff\Shelly\Software\ESP32 Sketchpad\TOF Development\ESP32_SPAD_Attempt1\ESP32_Wrover_TOF2_debug2
    Tried to change the address is 0x41 (the returned address when using sensor.getAddress();" and 0x29 like in the Polulu examples that use the Arduino <VL53L1X.h> library. But 0x52 is the only address 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
2021-04-28 Updated Readme with more required libraries. ESP Websocket now compiles for ESP32.
2021-05-01 got time setting somewhat working
    long way to go, next up is getting back IMU data with proper timestamp and header info
2021-05-02 IMU data not publishing correctly
    But we are making progress!
    [DevKit.ino]
2021-05-02 Got Quaternion working
    everything else is still not working great
    [DevKit.ino]
2021-05-02 got IMU working fully
    Now gotta ensure data makes sense, and is output in correct units!
    [DevKit.ino]
2021-05-02 fixing silly error
    it's not a pointer.... :-1:
    [DevKit.ino]
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2021-05-07 Starting TOF SPAD Development on Shelly Dev Kit
    \Software\ESP32 Sketchpad\TOF Development\ESP32_SPAD_Attempt2 takes the i2c_scanner.ino and adapts it slowly to include libraries to help get SPAD data from VL53L1X. Plan is to get continuous data fr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
2021-05-07 Able to initialized Dev Kit VL53L1X using Pololu <VL53L1X.h>sensor.init() function
    See Software\ESP32 Sketchpad\TOF Development\ESP32_SPAD_Attempt2
    Just initialized the sensor successfully without using "sensor.setTimeout(500);" <-- I'm worried this might cause the sensor to freeze.
    Next step is to use
    sensor.setDistanceMode(VL53L1X::Long);
    sensor.setMeasurementTimingBudget(50000);
2021-05-08 non-SPAD specific continuous reading works on ESP32_SPAD_Attempt2.ino
    In Software\ESP32 Sketchpad\TOF Development\ESP32_SPAD_Attempt2
    the code is able to get general continuous readings from VL53L1X
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2021-05-08 Able to use vl53x-st-api.ino libraries
    In Software\ESP32 Sketchpad\TOF Development\ESP32_SPAD_Attempt4, using ST libraries to get original ROI offset calibration data from Dev Kit TOF:
    orig top leftX: 15
    orig top leftY: 0
    orig bot rightX: 15
    orig bot rightY: 0
    Device ID:
    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
2021-05-10 ongoing work :)
    [Shelly.urdf.xacro]
2021-05-11 added cmd_vel Twist subscriber
    not doing anything with it yet except printing it
2021-05-12 Dev kit SPAD Assignment WORKS!
    using the new (and simple!) setROISize() and setROICenter() from the updated Pololu arduino library from: https://github.com/pololu/vl53l1x-arduino, I'm able to set the ROi location and get data. Cod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
2021-05-12 Added hardware design files
    for the 3 PCBs we currently use
    Also removed old design
    [BOM_PartType-5V UPS for projects.csv, BOM_PartType-Shelly Dev Kit.xlsx, BOM_PartType-Shelly VL53L1C Carrier Board.xlsx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]
2021-05-12 Wifi connectivity working on Saad's Dev Kit with TOF code
    able to connect to home wifi in Software\ESP32 Sketchpad\TOF Development\ESP32_SPAD_Attempt7 along with working TOF single SPAD code
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2021-05-16 updated to fix JSON issues
    now ready to use
    [ESP32_SPAD_Attempt7.ino]
2021-05-16 moved ROS code into it's own folder
    ongoing work
    [Shelly.urdf.xacro]
2021-05-16 renamed folder
    [shelly.urdf]
2021-05-16 Change folder names
    to remove spaces and replace with _
    [VL53L1X_ULD_API_Example Run.cfg, shelly.urdf]
2021-05-18 re-organized ROS folders
    more in line with ROS expectations/conventions
    [shelly.urdf]
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2021-06-02 Able to calculate averages for each SPAD
    Still need to save in data in the EEPROM
    see Software\ESP32_Sketchpad\TOF Development\Calibration_Attemp1
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2021-07-03 ESP32_SPAD_Attempt7.ino now uses EEPROM saved offset values to correct TOF readings
    \Software\ESP32_Sketchpad\TOF Development\ESP32_SPAD_Attempt7.ino now uses the calibrated offsets saved in EEPROM to correct the TOF readings. User should uncomment and run the function "calibrate_allspads()" when the TOF sensor is looking at a flat wall 140mm away. Full instructions on how to calibrate can be found in \Software\ESP32_Sketchpad\TOF Development\How to Calibrate the VL53L1X.docx
    [ESP32_SPAD_Attempt7.ino]

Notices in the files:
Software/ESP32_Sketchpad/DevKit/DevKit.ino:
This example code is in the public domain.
